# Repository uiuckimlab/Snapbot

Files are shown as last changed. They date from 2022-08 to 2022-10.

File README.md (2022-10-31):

# SNAPBOT 2.0
<div align="center">

</div>

-----------------
**Snapbot** is a reconfigurable legged robot to emulate configuration changes and various styles of legged locomotion. **Snapbot V2.0** has upgraded hardware to improve dynamical performance and robustness of the system for repetitive, and dynamical operations. 

Snapbot consists of a body and leg modules. The body modules includes a computer, batteries, electronic circuit boards, and a camera module. The camera module has 2-DOF, which can be used to recognize the robot's configuration or see surroundings. The leg module can be attached and detached to the body using magnetic connection, so it doesn't need any fastners but the docking structure ensures sturdy connection even during an impulsive motions. 

In this repository, we provide STL files and a BOM that is necessary to build the Snapbot V2.0 hardware, MATLAB Simscape simulation models, ROS package for the hardware, and URDF of the robot. 

## Contents
1. [3D printing STL](#3d-printing-stl)
2. [MATLAB Simulation](#matlab-simulation)
3. [ROS Package](#ros-package)
4. [Related Work](#related-work)
5. [Citation](#citation)

## 3D printing STL
STL files are provided in "3D printing STL" folder. The parts can be printed using most of 3D printing methods (FDM, SLS, SLA, etc.). The folder also contains the BOM (Bill of Materials) which lists the off-the-shelf components needed to build the Snapbot2.0 hardware. 

Currently there are two different head designs:
1. Default head


2. Babyface head


"3D printing STL/Head" folder has subfolders of two heads including the head cover and motor brackets. 

## MATLAB Simulation


Simulation model for Snapbot V2 was created using MATLAB Simscape multi-body (MATLAB 2021a). There are three simulations models for 2 leg, 4 leg, and 6 leg configuration with the motion generator implemented in the [paper](#citation).

## ROS Package
ROS package used to operate Snapbot V2 is provided with URDF file and meshes. By executing launch file "snapbot.launch", the robot can be teleoperated using keyboard inputs.

## Related Work

- [**Snapbot: A reconfigurable legged robot**](https://ieeexplore.ieee.org/abstract/document/8206477)
- [**Trajectory-based Probabilistic Policy Gradient for Learning Locomotion Behaviors**](https://ieeexplore.ieee.org/abstract/document/8794207)
- [**Automated Deep Reinforcement Learning Environment for Hardware of a Modular Legged Robot**](https://ieeexplore.ieee.org/abstract/document/8442201)
 
<!-- @INPROCEEDINGS{8206477,
  author={Kim, Joohyung and Alspach, Alexander and Yamane, Katsu},
  booktitle={2017 IEEE/RSJ International Conference on Intelligent Robots and Systems (IROS)}, 
  title={Snapbot: A reconfigurable legged robot}, 
  year={2017}}

@INPROCEEDINGS{8442201,  
  author={Ha, Sehoon and Kim, Joohyung and Yamane, Katsu},  
  booktitle={2018 15th International Conference on Ubiquitous Robots (UR)},   
  title={Automated Deep Reinforcement Learning Environment for Hardware of a Modular Legged Robot},   
  year={2018}}

@INPROCEEDINGS{8794207,  
  author={Choi, Sungjoon and Kim, Joohyung},  
  booktitle={2019 International Conference on Robotics and Automation (ICRA)},   
  title={Trajectory-based Probabilistic Policy Gradient for Learning Locomotion Behaviors},   
  year={2019}}
 -->

## Citation
```
@INPROCEEDINGS{9341279,  
  author={Gim, Kevin G. and Kim, Joohyung},  
  booktitle={2020 IEEE/RSJ International Conference on Intelligent Robots and Systems (IROS)},   
  title={Snapbot V2: a Reconfigurable Legged Robot with a Camera for Self Configuration Recognition},   
  year={2020}
}
```
Link: https://ieeexplore.ieee.org/abstract/document/9341279

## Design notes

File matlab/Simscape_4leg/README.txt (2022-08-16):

Simscape Multibody Contact Forces Library
Copyright 2014-2019 The MathWorks, Inc.

This library contains contact force models for use with Simscape Multibody.
They can be used for intermittent contact (parts bouncing off each other)
and persistent contact (parts resting on each other).  

You are welcome to use this library in your own projects. If you need to 
include the library in your own project, run >> CFL_SaveLibsOnly.m from 
the root directory of your local repository.  Only the critical files
will be copied to a folder "CFL_Libs", and you can cut-and-paste that
to your own local project.  Please cite

General approach for using this library:
   1. Identify the parts in your system that will hit each other during simulation

   2. Figure out which edges or surfaces will touch.  
      The contact models provided allow you to model contact between combinations
      of connected circular arcs with straight lines (2D) 
      and spheres with flat planes or cylinders (3D).

   3. Add reference frames for the lines and arcs that will touch.

   4. Add the correct contact force model between the two frames.

See the examples to understand how they are used.

Recommendations:
   1. Start with stiffness of 1e4 and damping of 1e2 and adjust from there.
   2. Use solver ode15s, Relative Tolerance = 1e-4, Absolute Tolerance = 1e-5
       and set the maximum step size to 1e-2.
   3. If you get unexpected behavior (parts flying through one another, 
       system gaining energy) your tolerances are not small enough.
       Reduce tolerances by a factor of 10 and max step size by a factor of 10
       until you get expected behavior.  Reducing stiffness and increasing damping
       can also help.

#########  Release History  #########
v 4.1(R2019a)   Mar 2019       Updated v4.1 for R2019a
                               Minor changes to accommodate physical signal units

v 4.1(R2018b)   Nov 2018       Added two examples
     (R2018a)   
     (R2017b)   1. New example Caster_4_Whl.slx
     (R2017a)      Models a four-wheel cart with casters on front wheels 
     (R2016b)
     (R2016a)   2. New example sm_build_spheres_in_sphere
     (R2015b)      MATLAB code to automatically assemble a model that has 
     (R2015a)      a user-defined number of spheres inside a sphere with
                   contact forces between all inner spheres and between 
                   inner spheres and outer sphere.

v 4.1(R2018b)   Sep 2018       Updated v4.1 for R2018b
                               All v4p1 have updated Extr_Data_Cam_Roller_Curve.m

     (R2018a)   Mar 2018       Tread example, walking robot example 
     (R2017b)
     (R2017a)   1. Adjusted Sphere to Belt Force (in 3D, Composite Forces)
     (R2016b)      Changed orientation of reference frame for the two
     (R2016a)      Sphere to Tube Enabled Forces. Z-axis flipped 180 deg
     (R2015b)      so that vx and wz inputs have the same sign. 
     (R2015a)   
                2. Adjusted sm_tread_drive example.slx
                   Uses adjusted Sphere to Belt Force, test sequence altered
                   to show turning and show both treads striking bump in 
                   forward and reverse. 

                3. New example sm_robot_6legs_4bar.slx 
                   Models 6-legged robot. Legs on each side are a pair of
                   connected four-bar linkages. Shows how to model robot
                   walking on uneven surface.   

                4. Added CFL_contact_setModel.m
                   Function to select force law in all contact forces in model.

                5. Additions to support Parts_Lib.slx 
                   Extrusion file Extr_Data_TriangleRounded_Holes.m and 
                   various images for masking parts.

v 4.0(R2018a)	Mar 2018       Updated for R2018a
     (R2017b)
     (R2017a)   1. Added Sphere to Tube Enabled Force
     (R2016b)      Sphere to Tube force that can be enabled/disabled
     (R2016a)      and can be used to model the ends of a driven conveyor belt.
     (R2015b)
     (R2015a)   2. Added Sphere to Belt Force (in 3D, Composite Forces)
                   Used to models spheres on a moving conveyor belt.  Can
                   also be used to model vehicles that ride on treads
                   like a bulldozer.  See sm_tread_drive  

                3. New examples sm_tread_drive, Frict3D_Balls_on_Driven_Tube 
                   These examples use Sphere to Tube Enabled Force and
                   Sphere to Belt Force. 

                4. Added sm_ball_bearing_testrig example
                   Models a ball bearing with variants that use
                   Common Gear Constraint (ideal) and contact forces
                   (permits vibration).

                5. Added extrusion script Extr_Data_Block_NotchCircle.m 
                   Used to calculate cross-sectional profile for inner and
                   outer race in Ball Bearing Testrig example

v 3.9 (R2017b)	Jan 2018       Added Cam Roller Constraint
                1. Added Cam Roller Constraint.  
                   Uses Point-on-Curve Constraint to model circular
                   roller on a cam with arbitrary profile.

                2. Added Extr_Data_Cam_Roller_Curve.m to calculate
                   path of Point-on-Curve Constraint.

                3. Added Cam_Follower_Constraint example.

v 3.8 (R2017b)	Sept 2017      Updated for R2017b

v 3.7 (R2017a)	July 2017      Sphere to Cone Force, many fixes
      (R2016b)		           Library saved in versions R2015b through R2017a
      (R2016a)
      (R2015b)
                1. Added Sphere to Cone Force.  Contact force is active on
		        inside and outside of cone.  Also added extrusion script
		        Extr_Data_Frustrum_Conical.m and example 
                Coll3D_08_Ball_in_Spinning_Cone.slx

                2. Sphere to Tube Force - fixed relative velocity calculation in
                Contact_Forces_Lib/3D/Sphere to Tube Force/Forces/Ff/vTan
                Previous releases delivered incorrect results if the cylinder
                could spin.  Added new example Coll3D_07_Balls_and_Sliding_Tube.slx

                3. Extr_Data_Box.m: functional change, parameters are full width
                and height instead of half width and half height.  Affected
                parameters within a few examples, such as Spinning Boxes

                4. Extr_Data_Cam.m: Changed to Extr_Data_Cam_Circles.m, which has
                two additional parameters (radii of holes).  Affected example
                Cam Follower and the UI for parameterizing the cam.

                5. Many 2D contact forces have been modified so that they
		        no longer refer to the World frame.  This permits them to be
                used in any plane, not just the x-y plane.

                6. Circle to Ring Force: calculations adjusted to use consistent
                distance to contact point for circle and ring.  May result in
                minor changes to simulation results.

                7. Mask commands adjusted - eliminated imread(), use option
                "Opaque with ports" (R16a and above), and other settings.

v 3.6 (R2017a)	Mar  2017       Updated for R2017a
      (R2016b)	
                1. New example: Ball on Wheel with Controller (2D Friction Examples)
                   Models a ball balanced on a wheel.
                2. Removed MATLAB variables from blocks in Contact_Forces_Lib.slx
                   Some library elements contained MATLAB variables in the dialog box
                   parameters on the Dimensions and Visual tab.  These were replaced
                   with hardcoded default values to avoid warnings about undefined variables.
                3. Additional parameters were added to the Sphere block in Parts_Lib.slx 
                   to enable the marks to be shown or hidden per axis. 
                4. New script CFL_SaveLibsOnly.m that copies only the critical files 
        		   of this repository to a new folder so you can include them in
                   your own project.

v 3.5 (R2016b)	Jan  2017	3D Composite Forces, Sphere-to-Plane Enabled
                1. Added Face-to-Plane in 3D/Composite Forces.  This is useful for
                   two flat square surfaces that may contact each other at arbitrary 
                   angles.  It assumes no edges will intersect (one square is 
                   significantly larger than the other
                2. Added Face-to-Belt-Faces forces in 3D/Composite Forces.  This is
                   useful for modeling 3D boxes on conveyor belts where only one
                   face of the box will encounter the belt.  It accepts the 
                   speed of the belt as an input signal (vx and/or vy)
                3. Added Sphere-to-Plane Enabled Force.  This is used within the
                   composite force´Face-to-Belt-Faces composite force
                4. Added example Gripper with Conveyor Belts (3D Applications). 
                   Uses the new forces to model a box that is transferred by a 
                   gripper between two conveyor belts.  One belt brings the box
                   to the gripper, the other moves it away.

		Additional parameters were added to the Cylinder block 
                in Parts_Lib.slx to enable arbitrary colors for the cylinders.

v 3.4 (R2016b)	Sep  2016	Updated for R2016b
		1. Fixed outputs for Circle-to-Ring, Sphere-to-Tube, Sphere-to-Plane
		   Force output signals for these signals now go to zero when 
		   circle/sphere leaves active range for force, where active range is 
		   an arc of the ring/tube or length of the plane. Previously, the
		   measured value for the force would be held if the force was active
		   as the circle/sphere left the active range for the force.

		2. Copy for Merge block added in Sphere-to-Plane block
		   This block is necessary in some configurations.

v 3.3 (R2016a)	Apr  2016	Added optional visualization for contact surfaces
		The surfaces associated with the contact forces can now be visualized.	
		This helps you confirm you have oriented the surfaces properly and
		defined them to be an appropriate length or active range of angles.

		All contact forces now have an additional tab labeled "Visual".  On
		this tab you can enable a visualization of the surface, which is done
		using a Solid with density set to 0.  For the 2D contact forces you 
		will need to define the length of the surface along the z-axis of
		the contact force and it is used for visualization purposes only. 
		You can show/hide all contact surfaces in the model using the
		new function CFL_visual_setOnOff.m in the Scripts_Data directory.

		Additionally in this release, a number of plotting scripts have been
		added to the examples, and in many cases the variables used by
		the example were moved to the Model Workspace.

v 3.2 (R2016a)	Mar  2016	Disabled zero crossings in some Abs blocks
      (R2015b)  Affects Circle-to-Finite Line, Sphere to Finite Plane
		The zero-crossings in Abs blocks used to check the displacement
                of the circle/sphere reference frame from the line/plane
		reference frame along the line/surface (y / xy) direction is
		not necessary.  When the line/plane can move along the (y / xy)
 		direction, it can lead to excessive zero crossings, slowing down
		the simulation.

v 3.1 (R2016a)	Mar  2016	Renamed Simscape Multibody Contact Forces Library
		1. Geneva drive model imported from CAD is now parameterized

v 3.0 (R2015b)  Sept 2015	Updated to R2015b

v 3.0 (R2015a)  July 2015	3D models added
                1. Sphere-to-Sphere, Sphere-in-Sphere, Sphere-to-Plane, 
                   Sphere-to-Tube added, all with optional friction model
                2. Added 3D collision and friction examples
		3. Added Two Wheel Robot example (3D Applications)

                (2D Models)
                4. Modified 2D enabled forces
		   ** Change from v2.0 -- may require you to update your models ** 
                   Modified Circle to Circle Force Enabled, 
                   Circle to Finite Line Force Enabled to use a bus as the
                   input signal instead of signal input.  Bus permits user to
                   optionally define enabled/disabled, and to set velocity
                   perpendicular to normal force (vy).  Primary use is for ideal 
                   models of conveyor belts.
                5. Added 2D/Composite forces (Box to Box force, Box to Belt force)
                6. Added Belts_01_Two_Belts.slx (simple conveyor belt example)
                
                Documentation, Dialog boxes
                7. Updates to all dialog boxes (added images, fixed prompts and description)
                8. Documentation revised                

v 2.0 (R2014a)  September 2014	Friction model added
                1. Added optional friction model (Stick-Slip Continuous)
		   to Circle to Circle, Circle to Finite Line, Circle to Ring
                2. Added all Friction_* examples 
                3. Added Spinning Boxes example 
                   Shows box-to-box contact force
                4. Fixed callback commands, all contact force blocks
		   Set variant in Initialization commands instead of mask callbacks
                5. Fixed Circle to Finite Line, Circle to Finite Line Enabled
                   Force on line was applied in wrong reference frame

v 1.0 (R2014a)  August 2014     Initial release.
		Circle-Circle (Enabled), Circle-Line (Enabled), Circle-Ring
		7 Simple, Cam Follower, Geneva Drive. Mini Golf compatible

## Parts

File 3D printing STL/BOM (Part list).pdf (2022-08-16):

Parts List

Leg
Part | Motor | Idler | Ball bearings
Model | Dynamixel XM430-W210-T (https://www.robotis.us/dynamixel-xm430-w210-t/) | Robotis HN12-I101 set (https://www.robotis.us/hn12-i101-set/) | SMR128ZZ A5 (http://www.metsorj.com/ProductDetails.asp?ProductCode=E4W336)
Quantity | 12 (2 per leg) | 12 (2 per leg) | 12 (2 per leg)

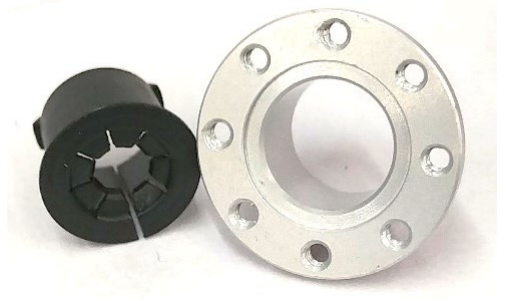
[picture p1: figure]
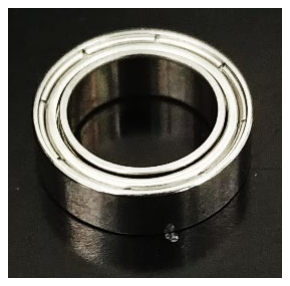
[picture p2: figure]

Image

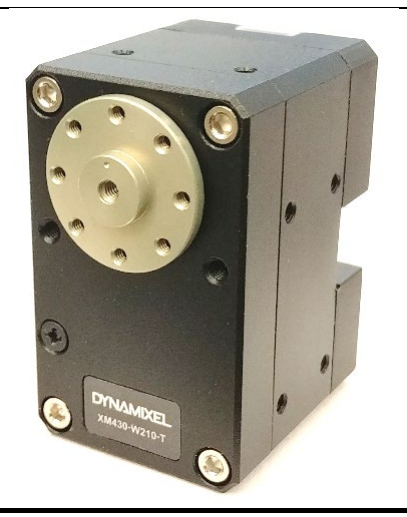
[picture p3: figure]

Custom Electronics
Wires
For connection ports
Part (for:) | Connector housing
Power board | Leg motor | Connection port
Model | Molex 0050375033 (https://www.digikey.com/en/products/detail/molex/0050375033/280419) | Molex 0510650300 (https://www.digikey.com/en/products/detail/molex/0510650300/403567) | Molex 0510650400 (https://www.digikey.com/en/products/detail/molex/0510650400/403568)
Quantity | 6 | 6 | 12

Image

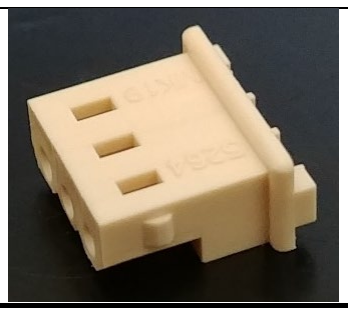
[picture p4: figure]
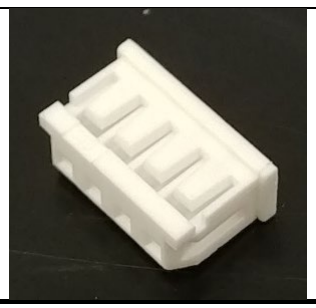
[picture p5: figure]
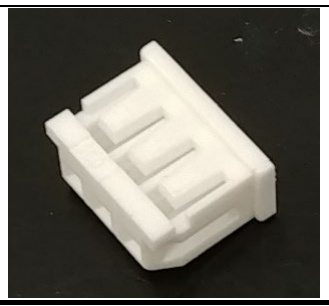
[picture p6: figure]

Part (for:) | Terminal
Connection port; leg motor | Power board
Model | Molex 0502128000 (https://www.digikey.com/en/products/detail/molex/0502128000/2524899) | Molex 0008701039 (https://www.digikey.com/en/products/detail/molex/0008701039/765268)
Quantity | 54 | 18

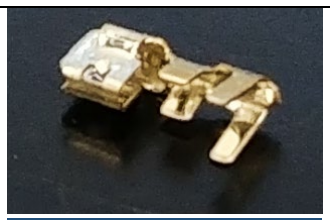
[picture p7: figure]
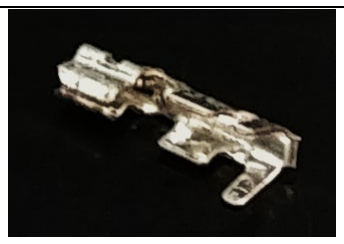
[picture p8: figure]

Image

***Following are intertwined and go into terminal block***

For power board / battery

Part | Battery connector
Model | Finware AMASS XT30U-M (https://www.tme.com/us/en-us/details/xt30u-m/dc-power-connectors/amass/)
Quantity | 2


Image

For regulators

Part (for:) | Connector housing | Terminal
5V regulator | 7.5V regulator | Both regulators
Model | JST EHR-3 (https://www.digikey.com/en/products/detail/jst-sales-america-inc/EHR-3/527225) | JST EHR-4 (https://www.digikey.com/en/products/detail/jst-sales-america-inc/EHR-4/527226) | JST SEH-001T-P0.6 (https://www.digikey.com/en/products/detail/jst-sales-america-inc/SEH-001T-P0-6/527267)
Quantity | 1 | 1 | 7

Image


Part (for:) | Connector header
5V regulator | 7.5V regulator
Model | JST B3B-EH-A(LF)(SN) (https://www.digikey.com/en/products/detail/jst-sales-america-inc/B3B-EH-A-LF-SN/926521) | JST B4B-EH-A(LF)(SN) (https://www.digikey.com/en/products/detail/jst-sales-america-inc/B4B-EH-A-LF-SN/758748)
Quantity | 1 | 1


Image

Connection Ports

Part | Spring-loaded connector (male) | Spring-loaded connector (female) | Connector header
Model | Mill-Max 823-22-008-10- (https://www.digikey.com/en/products/detail/mill-max-manufacturing-corp/823-22-008-10-002101/1146974)002101 (https://www.digikey.com/en/products/detail/mill-max-manufacturing-corp/823-22-008-10-002101/1146974) | Mill-Max 419-10-208-00- (https://www.digikey.com/en/products/detail/mill-max-manufacturing-corp/419-10-208-00-006000/5176111)006000 (https://www.digikey.com/en/products/detail/mill-max-manufacturing-corp/419-10-208-00-006000/5176111) | Molex 0532530470 (https://www.digikey.com/en/products/detail/molex/0532530470/965998)
Quantity | 6 | 6 | 12

Image


The connection ports also require a custom PCB. A CAD model and a circuit diagram are provided. Twelve of these PCBs need to be printed.

Power Board

Part | Connector header (leg) | Connector header (camera) | Terminal block
Model | Molex 0022035035 (https://www.digikey.be/product-detail/en/molex/0022035035/900-0022035035-ND/403302) | Molex 0532530370 (https://www.digikey.com/en/products/detail/molex/0532530370/965997) | TE Connectivity 282834-2 (https://www.digikey.com/en/products/detail/te-connectivity-amp-connectors/282834-2/1150135)
Quantity | 7 | 1 | 2

Image


The power board is a custom PCB. A CAD model and a circuit diagram are provided. Only one of these PCBs is required.

Body
Orange Pi Lite
SD card (16 GB)
Camera
U2D2 dongle
Voltage regulators (7.5V, 5V)

Other necessary stuff

22 AWG wire
18 AWG wire (for battery connector) (Wire with female connector for orange pi) Solder
Soldering iron
Screws
Magnets
Wire crimper
Wire cutter/stripper
Allen key: M2, M2.5, M3
Pliers
3d printer + material
Heat shrink / tape
Hot glue gun

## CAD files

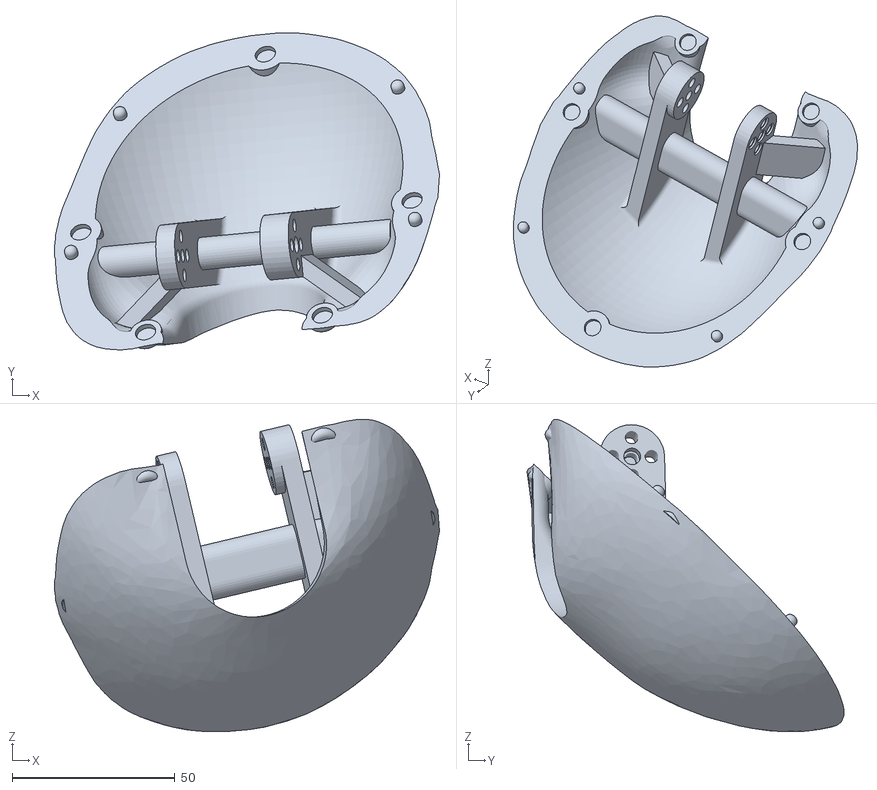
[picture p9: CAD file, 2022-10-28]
3D printing STL/Head/Babyface/Babyface_bracket.STL
118.2 x 97.3 x 95.9

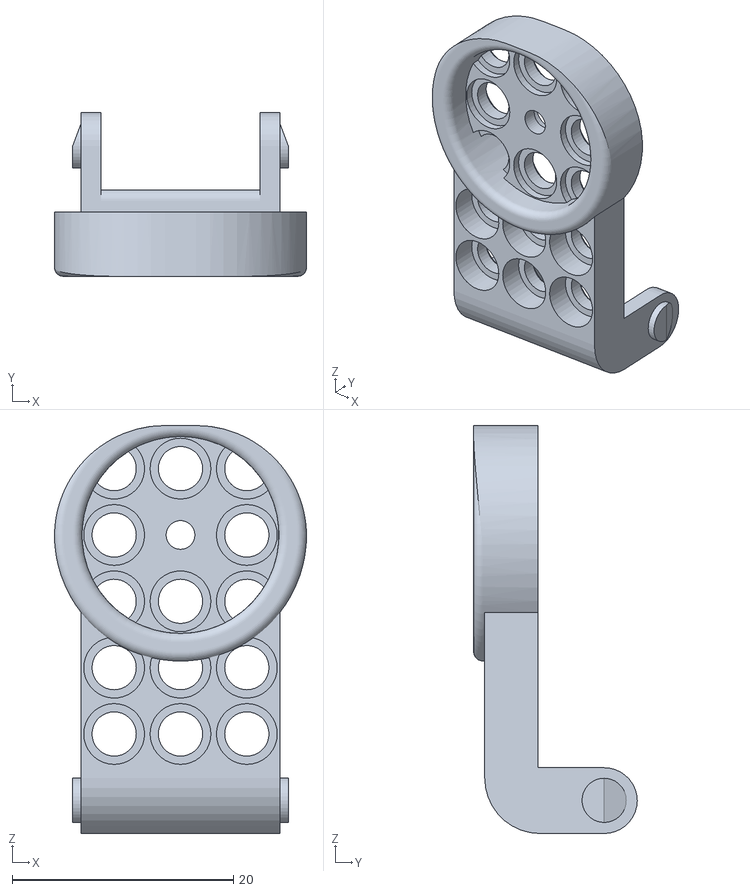
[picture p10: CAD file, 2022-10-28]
3D printing STL/Head/Default/Camera_plate_yaw.STL
22.8 x 14.8 x 36.9

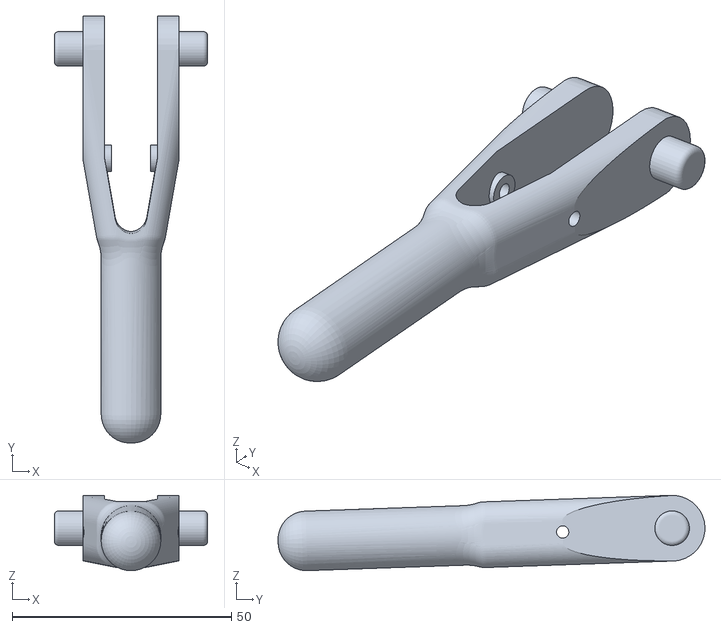
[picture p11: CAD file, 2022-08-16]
3D printing STL/Leg_part_05.STL
35.0 x 97.5 x 17.2

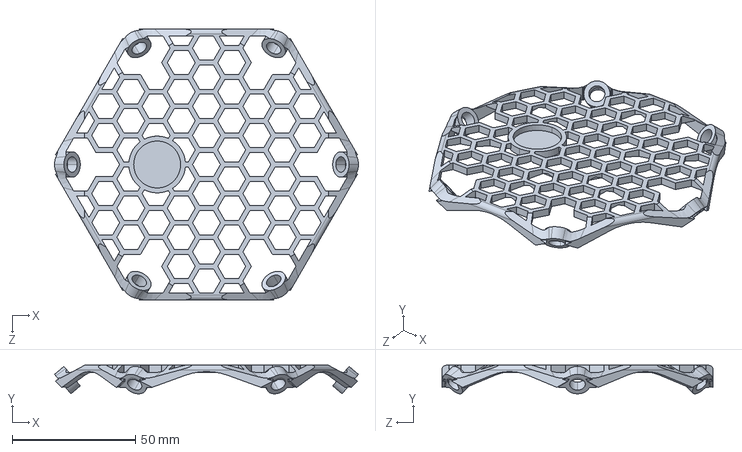
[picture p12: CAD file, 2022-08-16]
matlab/Simscape_2leg/cover_IMU_Default_sldprt.STEP
123.2 x 11.6 x 110.0 mm

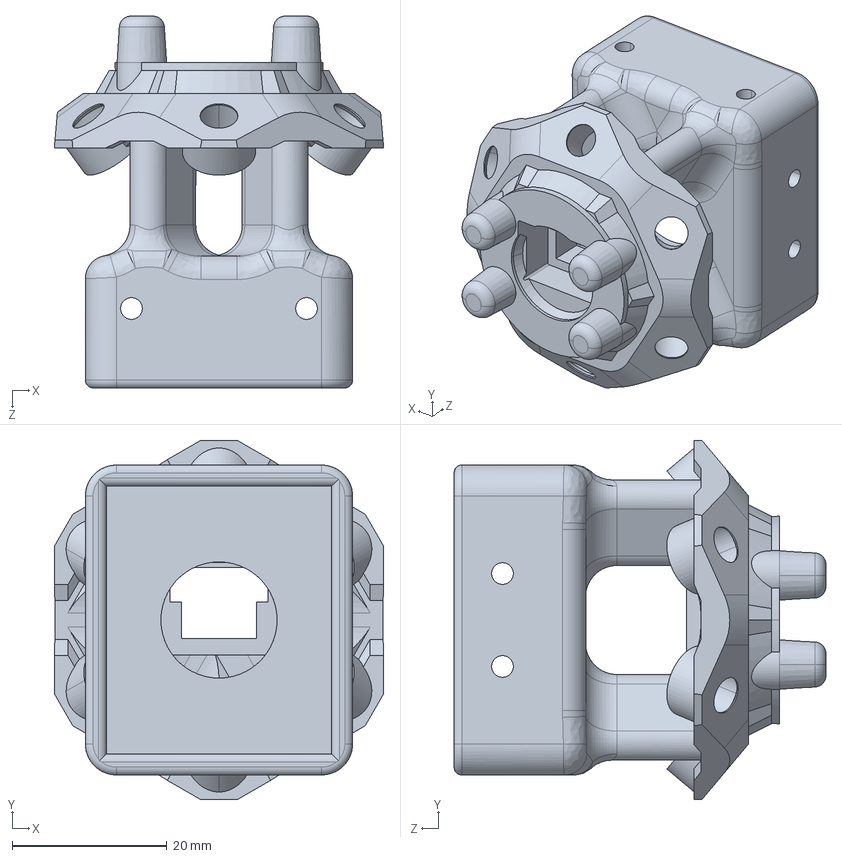
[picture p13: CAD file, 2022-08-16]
matlab/Simscape_6leg/Leg_part_01_yaw_Default_sldprt.STEP
42.5 x 46.3 x 48.0 mm

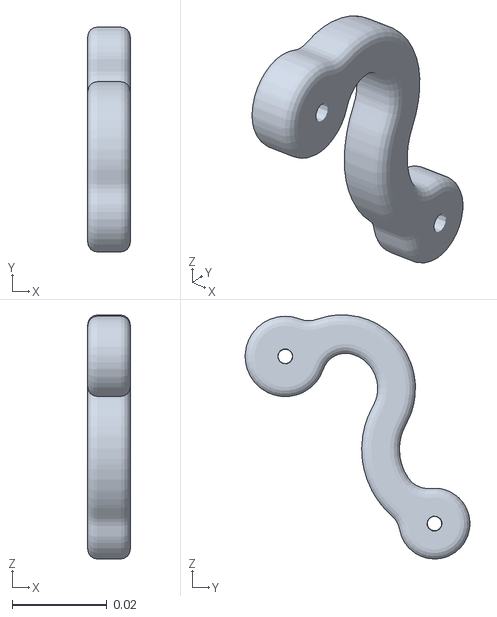
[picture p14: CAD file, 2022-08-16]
meshes/Leg_module_4_4bar.STL
0.009 x 0.0476 x 0.0516

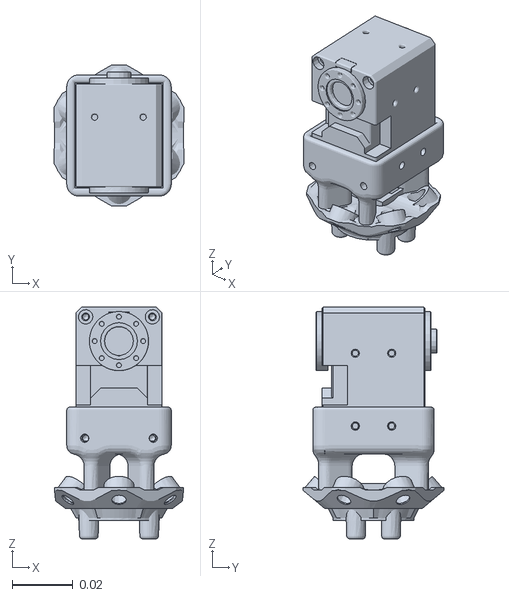
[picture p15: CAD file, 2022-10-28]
URDF/URDF_babyface(10282022)/Snapbot_V2.0.SLDASM/meshes/Leg_module_1_1.STL
0.0427 x 0.0466 x 0.0765

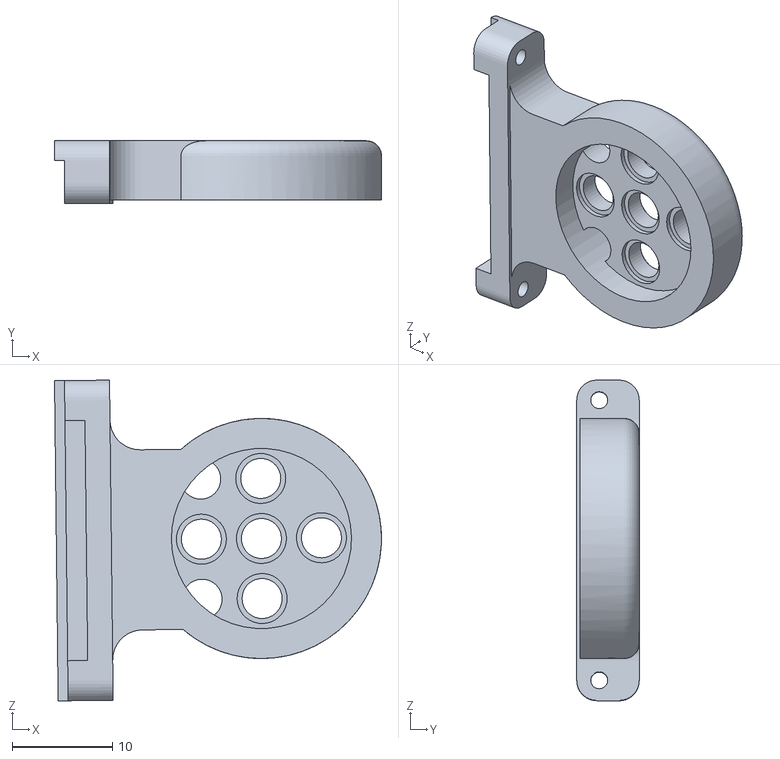
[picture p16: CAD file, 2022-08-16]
3D printing STL/Camera_bracket_2.STL
32.7 x 6.25 x 32.1

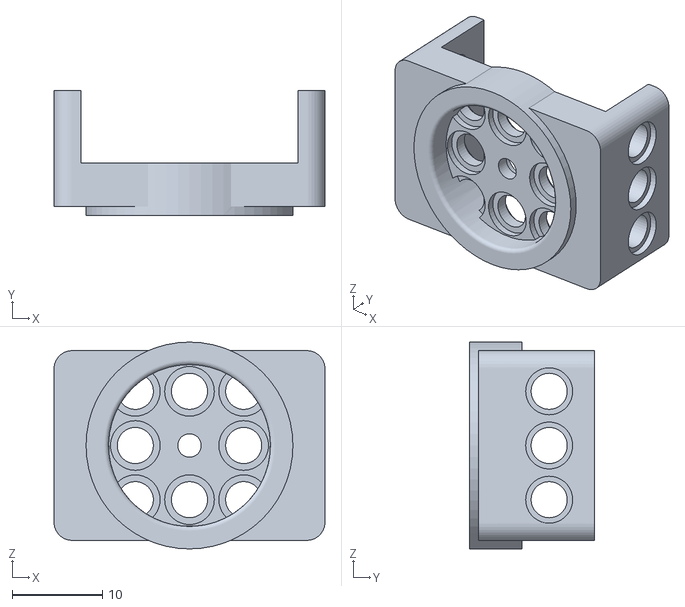
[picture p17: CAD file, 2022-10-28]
3D printing STL/Head/Babyface/Yaw_motor_bracket.STL
30.0 x 13.8 x 22.9

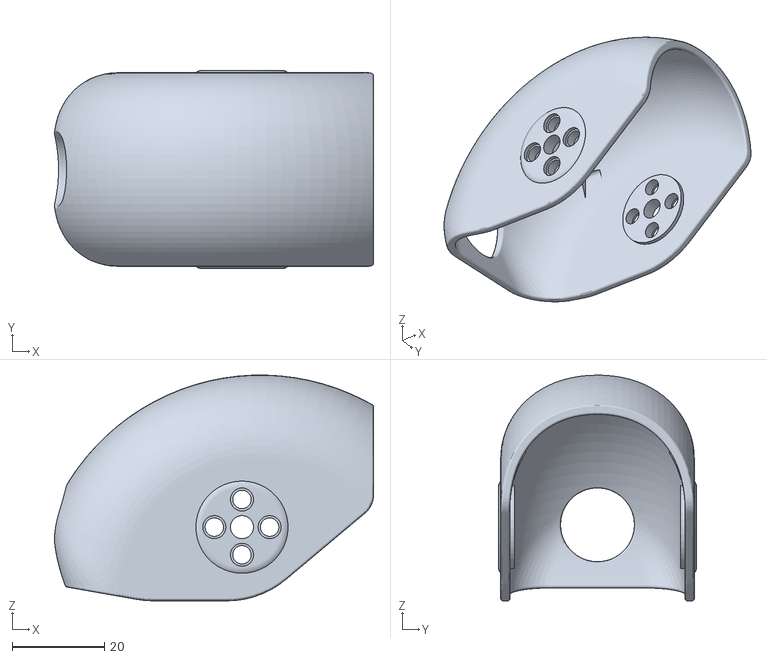
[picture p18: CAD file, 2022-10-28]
3D printing STL/Head/Default/Snapbot_Head.STL
69.2 x 43.0 x 49.0

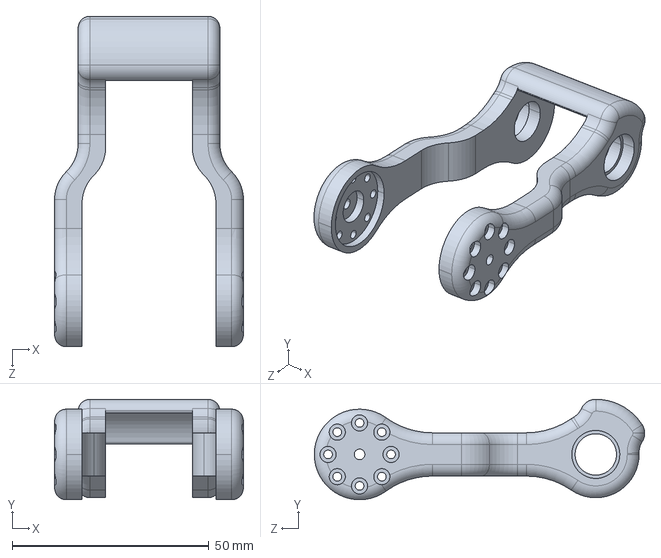
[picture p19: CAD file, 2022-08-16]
matlab/Simscape_2leg/Leg_part_04_Default_sldprt.STEP
48.0 x 25.5 x 83.9 mm

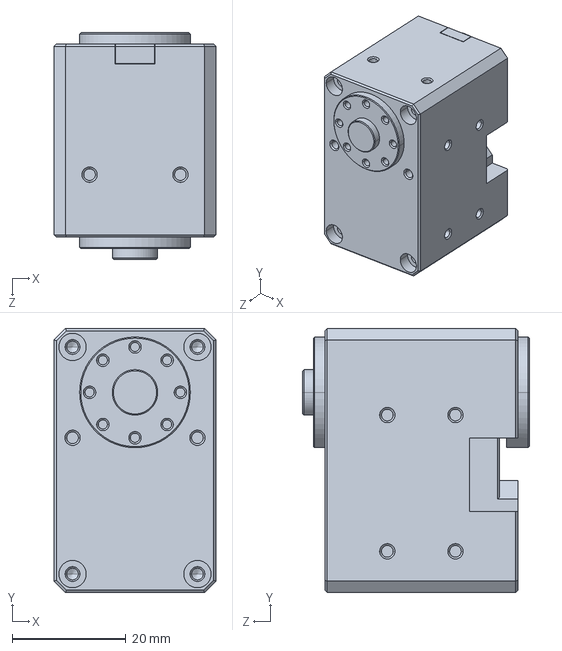
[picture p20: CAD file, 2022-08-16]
matlab/Simscape_6leg/v4_Hyb_X-430_IDLE_uncut_Default_sldprt.STEP
28.5 x 46.5 x 39.9 mm

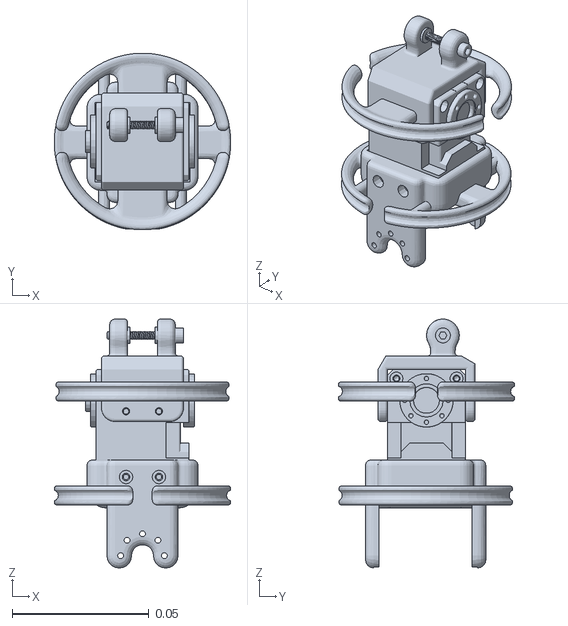
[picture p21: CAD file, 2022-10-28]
URDF/URDF_Default (10282022)/Snapbot_V2.0.SLDASM/meshes/Leg_module_1_2.STL
0.0645 x 0.0645 x 0.091

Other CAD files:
matlab/Simscape_4leg/cover_Default_sldprt.STEP
URDF/URDF_Default (10282022)/Snapbot_V2.0.SLDASM/meshes/Leg_module_2_4bar.STL
matlab/Simscape_4leg/cover_IMU_Default_sldprt.STEP
meshes/Leg_module_6_4bar.STL
URDF/URDF_babyface(10282022)/Snapbot_V2.0.SLDASM/meshes/Leg_module_2_4bar.STL
3D printing STL/Body - cover_V4-1.STL
3D printing STL/Body - cover_top_V4-1.STL
3D printing STL/Camera_bracket_1.STL
3D printing STL/Camera_bracket_3.STL
3D printing STL/Camera_cover.STL
3D printing STL/Head/Babyface/Babyface_Face.STL
3D printing STL/Head/Default/Camera_bracket_pitch_1.STL
3D printing STL/Head/Default/Camera_bracket_pitch_2.STL
3D printing STL/Leg_part_01.STL
3D printing STL/Leg_part_02.STL
3D printing STL/Leg_part_03.STL
3D printing STL/Leg_part_04.STL
3D printing STL/Leg_part_06.STL
URDF/URDF_Default (10282022)/Snapbot_V2.0.SLDASM/meshes/Body.STL
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

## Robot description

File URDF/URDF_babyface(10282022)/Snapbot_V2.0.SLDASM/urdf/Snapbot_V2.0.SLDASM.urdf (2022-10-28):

<?xml version="1.0" encoding="utf-8"?>
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
<robot name="Snapbot_V2.0.SLDASM">
  <link name="Body">
    <inertial>
      <origin xyz="0.000698393115871002 0.000288945802796733 0.0080342370525136" rpy="0 0 0" />
      <mass value="0.243375116892044" />
      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
    </inertial>
    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
  </link>
  <link name="Camera_module_1">
    <inertial>
      <origin xyz="-0.000174104745675234 0.000380109596667467 0.0231270475088353" rpy="0 0 0" />
      <mass value="0.0193486685182062" />
      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
    </inertial>
    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
  </link>
  <joint name="camera_1" type="continuous">
    <origin xyz="0 0 0.05" rpy="0 0 2.61799387799149" />
    <parent link="Body" />
    <child link="Camera_module_1" />
    <axis xyz="0 0 1" />
  </joint>
  <link name="Camera_module_2">
    <inertial>
      <origin xyz="0.00436630099388993 0.00301719279420027 0.0506803900992624" rpy="0 0 0" />
      <mass value="0.486270044594427" />
      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
    </inertial>
    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
  </link>
  <joint name="camera_2" type="continuous">
    <origin xyz="0 0 0.0183294742460734" rpy="-0.00940777862508587 0.0162930683068517 -7.6643050616781E-05" />
    <parent link="Camera_module_1" />
    <child link="Camera_module_2" />
    <axis xyz="0.500000000000001 -0.866025403784438 0" />
  </joint>
  <link name="Leg_module_1_1">
    <inertial>
      <origin xyz="-7.13724657916415E-08 0.000373799301046029 0.0154182546673216" rpy="0 0 0" />
      <mass value="0.0631785349056668" />
      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
    </inertial>
    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
  </link>
  <joint name="leg_1_1" type="fixed">
    <origin xyz="-0.0389249999999995 -0.0674200776846189 0.0103294742460734" rpy="1.5707963267949 0 -0.52359877559829" />
    <parent link="Body" />
    <child link="Leg_module_1_1" />
    <axis xyz="0 0 0" />
  </joint>
  <link name="Leg_module_1_2">
    <inertial>
      <origin xyz="-0.000290776360641745 0.000350553903850227 0.0424303561818182" rpy="0 0 0" />
      <mass value="0.0824270440491864" />
      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
    </inertial>
    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
  </link>
  <joint name="leg_1_2" type="continuous">
    <origin xyz="0 0 0.03725" rpy="0 0 0" />
    <parent link="Leg_module_1_1" />
    <child link="Leg_module_1_2" />
    <axis xyz="0 1 0" />
  </joint>
  <link name="Leg_module_1_3">
    <inertial>
      <origin xyz="2.45741484106166E-09 0.000972843111612401 0.036226536467209" rpy="0 0 0" />
      <mass value="0.0151486232431239" />
      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
    </inertial>
    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
  </link>
  <joint name="leg_1_3" type="continuous">
    <origin xyz="0 0.00029999999999997 0.05675" rpy="-0.0100573048452913 0 0" />
    <parent link="Leg_module_1_2" />
    <child link="Leg_module_1_3" />
    <axis xyz="1 0 0" />
  </joint>
  <link name="Leg_module_1_4">
    <inertial>
      <origin xyz="4.20295677225763E-05 -0.039054256810963 -0.001354432069402" rpy="0 0 0" />
      <mass value="0.0147333532003768" />
      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
    </inertial>
    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
  </link>
  <joint name="leg_1_4" type="continuous">
    <origin xyz="0 -0.000603428117922688 0.0599969655441553" rpy="-0.0105798453585739 0 0" />
    <parent link="Leg_module_1_3" />
    <child link="Leg_module_1_4" />
    <axis xyz="1 0 0" />
  </joint>
  <link name="Leg_module_1_4bar">
    <inertial>
      <origin xyz="-0.000153041712575408 -0.0147990308191147 0.0229851342034179" rpy="0 0 0" />
      <mass value="0.00683592925491238" />
      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
    </inertial>
    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
  </link>
  <joint name="leg_1_4bar" type="continuous">
    <origin xyz="0 0.00629999999999993 0.0804999999999999" rpy="-0.0165784581965256 0 0" />
    <parent link="Leg_module_1_2" />
    <child link="Leg_module_1_4bar" />
    <axis xyz="1 0 0" />
  </joint>
  <link name="Leg_module_2_1">
    <inertial>
      <origin xyz="-6.95475167594717E-08 0.00037379623691287 0.0154182547266335" rpy="0 0 0" />
      <mass value="0.063178534807664" />
      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
    </inertial>
    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
  </link>
  <joint name="leg_2_1" type="fixed">
    <origin xyz="0.038925000000001 -0.0674200776846179 0.0103294742460733" rpy="1.5707963267949 0 0.52359877559831" />
    <parent link="Body" />
    <child link="Leg_module_2_1" />
    <axis xyz="0 0 0" />
  </joint>
  <link name="Leg_module_2_2">
    <inertial>
      <origin xyz="-0.000290786260265109 0.000350550447493953 0.0424303491067431" rpy="0 0 0" />
      <mass value="0.0824270292833377" />
      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
    </inertial>
    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
  </link>
  <joint name="leg_2_2" type="continuous">
    <origin xyz="0 0 0.03725" rpy="0 0 0" />
    <parent link="Leg_module_2_1" />
    <child link="Leg_module_2_2" />
    <axis xyz="0 1 0" />
  </joint>
  <link name="Leg_module_2_3">
    <inertial>
      <origin xyz="6.11769995773059E-10 0.000972841972894574 0.0362265364557568" rpy="0 0 0" />
      <mass value="0.0151486232431239" />
      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
    </inertial>
    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
  </link>
  <joint name="leg_2_3" type="continuous">
    <origin xyz="0 0.000299999999999996 0.0567499999999999" rpy="-0.0100573048453112 0 0" />
    <parent link="Leg_module_2_2" />
    <child link="Leg_module_2_3" />
    <axis xyz="1 0 0" />
  </joint>
  <link name="Leg_module_2_4">
    <inertial>
      <origin xyz="4.19939626801757E-05 -0.0390541987134747 -0.00135443548203865" rpy="0 0 0" />
      <mass value="0.0147333946079412" />
      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
    </inertial>
    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
  </link>
  <joint name="leg_2_4" type="continuous">
    <origin xyz="0 -0.000603428117910471 0.0599969655441548" rpy="-0.0105798453581945 0 0" />
    <parent link="Leg_module_2_3" />
    <child link="Leg_module_2_4" />
    <axis xyz="1 0 0" />
  </joint>
  <link name="Leg_module_2_4bar">
    <inertial>
      <origin xyz="-0.000153041712573354 -0.0147990308191101 0.0229851342034186" rpy="0 0 0" />
      <mass value="0.00683592925491239" />
      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
    </inertial>
    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
  </link>
  <joint name="leg_2_4bar" type="continuous">
    <origin xyz="0 0.00629999999999995 0.0805" rpy="-0.0165784581965541 0 0" />
    <parent link="Leg_module_2_2" />
    <child link="Leg_module_2_4bar" />
    <axis xyz="1 0 0" />
  </joint>
  <link name="Leg_module_3_1">
    <inertial>
      <origin xyz="-7.06608178473466E-08 0.000373797728506917 0.0154182586742905" rpy="0 0 0" />
      <mass value="0.0631785313638385" />
      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
    </inertial>
    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
  </link>
  <joint name="leg_3_1" type="fixed">
    <origin xyz="0.0778499999999993 0 0.0103294742460734" rpy="1.5707963267949 0 1.5707963267949" />
    <parent link="Body" />
    <child link="Leg_module_3_1" />
    <axis xyz="0 0 0" />
  </joint>
  <link name="Leg_module_3_2">
    <inertial>
      <origin xyz="-0.000290780437123685 0.000350551822572993 0.0424303356191464" rpy="0 0 0" />
      <mass value="0.0824272438246167" />
      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
    </inertial>
    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
  </link>
  <joint name="leg_3_2" type="continuous">
    <origin xyz="0 0 0.03725" rpy="0 0 0" />
    <parent link="Leg_module_3_1" />
    <child link="Leg_module_3_2" />
    <axis xyz="0 1 0" />
  </joint>
  <link name="Leg_module_3_3">
    <inertial>
      <origin xyz="1.53462381789992E-09 0.00170127905765847 0.0361996388039809" rpy="0 0 0" />
      <mass value="0.0151486257339542" />
      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
    </inertial>
    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
  </link>
  <joint name="leg_3_3" type="continuous">
    <origin xyz="0 0.000300000000000003 0.0567499999999997" rpy="0.0100573048452967 0 0" />
    <parent link="Leg_module_3_2" />
    <child link="Leg_module_3_3" />
    <axis xyz="1 0 0" />
  </joint>
  <link name="Leg_module_3_4">
    <inertial>
      <origin xyz="4.20490632792337E-05 -0.039076824241083 0.000258194696472008" rpy="0 0 0" />
      <mass value="0.0147334003564446" />
      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
    </inertial>
    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
  </link>
  <joint name="leg_3_4" type="continuous">
    <origin xyz="0 0.000603428117812372 0.0599969655441564" rpy="0.0105798453584752 0 0" />
    <parent link="Leg_module_3_3" />
    <child link="Leg_module_3_4" />
    <axis xyz="1 0 0" />
  </joint>
  <link name="Leg_module_3_4bar">
    <inertial>
      <origin xyz="-0.000153041712520068 -0.0140289201388825 0.0234631009730389" rpy="0 0 0" />
      <mass value="0.00683592925491239" />
      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
    </inertial>
    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
  </link>
  <joint name="leg_3_4bar" type="continuous">
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

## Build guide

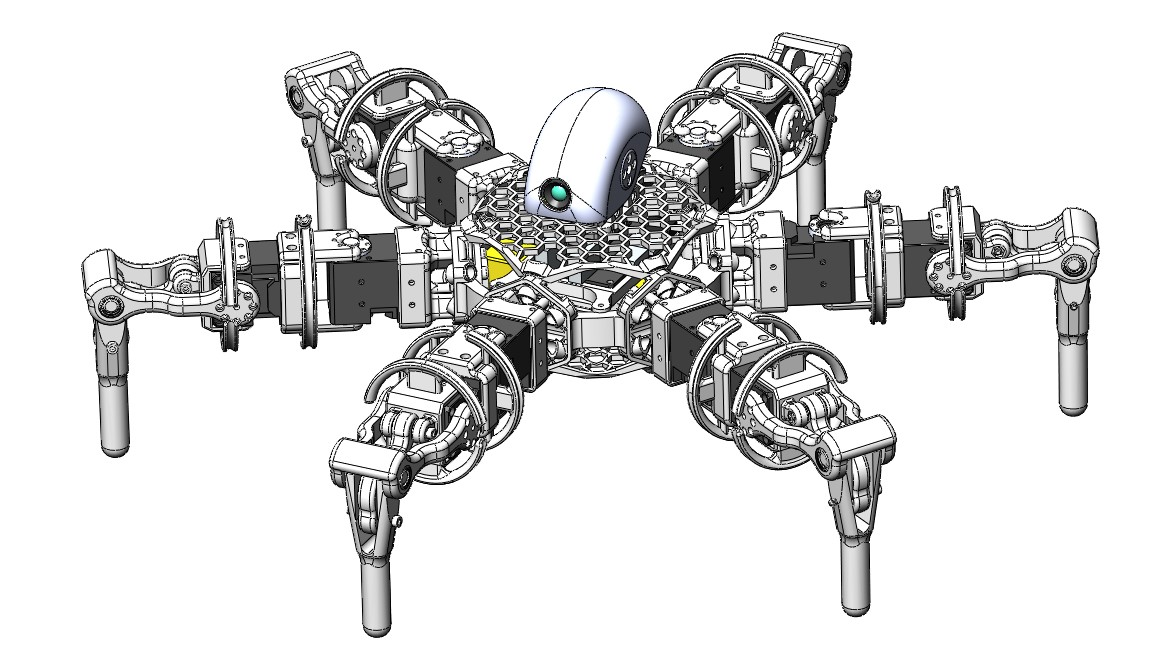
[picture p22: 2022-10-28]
3D printing STL/Head/Default_head.jpg

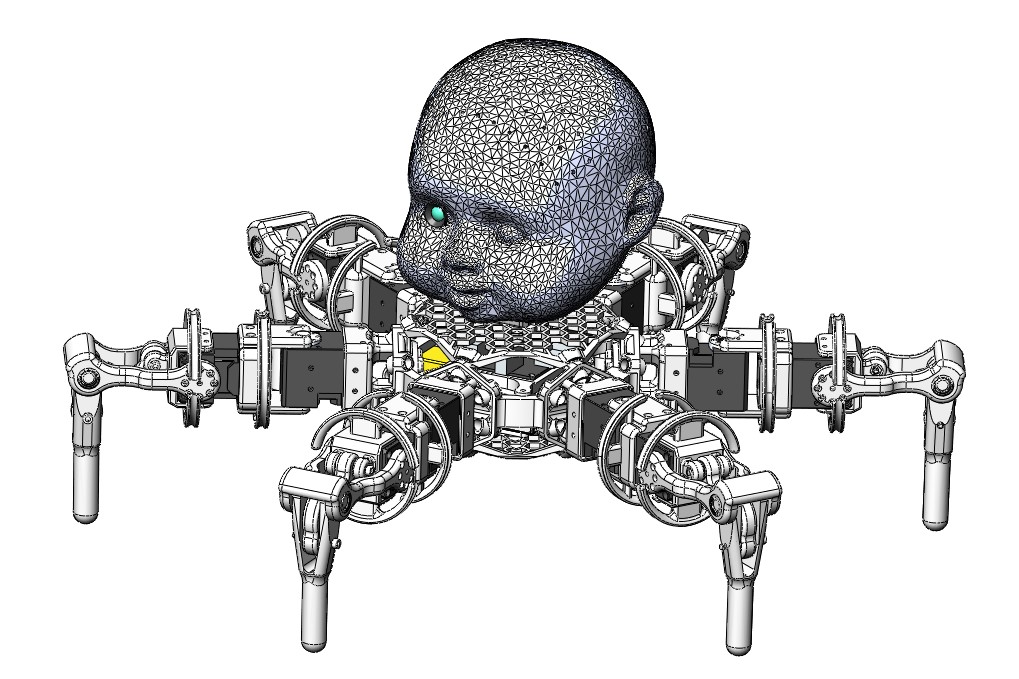
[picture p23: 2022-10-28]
3D printing STL/Head/Babyface_head.jpg

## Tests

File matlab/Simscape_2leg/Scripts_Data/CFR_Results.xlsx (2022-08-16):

 | Contact Forces Tests | 9.6.0.1072779 (R2019a) |  |  | 19-Mar-2019 07:07:34 |  | CFL v4.1
 |  |  | Linear, No Friction |  | Linear, Stick-Slip C |  | Nonlin., No Friction |  | Nonlin., Stick-Slip C
# | Model | Stop Time | # Steps | Sim Time | # Steps | Sim Time | # Steps | Sim Time | # Steps | Sim Time
1 | Collision_01_Ball_Infinite_Plane | 6.00 | 2388 | 1.18 | 2388 | 0.39 | 2388 | 0.47 | 2388 | 0.33
2 | Collision_02_Disk_Finite_Plane_Fixed | 4.00 | 669 | 0.56 | 935 | 0.18 | 718 | 0.15 | 1020 | 0.16
3 | Collision_03_Disk_Finite_Plane_Spin | 1.50 | 298 | 0.29 | 370 | 0.11 | 317 | 0.07 | 398 | 0.08
4 | Collision_04_Disks_in_Box | 3.00 | 3726 | 4.08 | 4928 | 5.10 | 5039 | 3.11 | 6295 | 4.05
5 | Collision_05_Disk_in_Ring | 5.00 | 2071 | 0.37 | 2660 | 0.77 | 2276 | 0.56 | 2954 | 0.65
6 | Collision_06_Catapult | 1.20 | 612 | 0.21 | 579 | 0.17 | 747 | 0.17 | 602 | 0.21
7 | Collision_07_Ball_Finite_Plane_Float | 1.50 | 210 | 0.08 | 213 | 0.04 | 221 | 0.06 | 223 | 0.05
8 | Collision_08_Compare_Forces | 5.00 | 9225 | 5.33 | 17963 | 6.91 | 10816 | 3.80 | 21376 | 10.73
9 | Friction_01_Box_on_Ramp_Constraint | 10.00 | 1137 | 0.17 | 1137 | 0.10 | 1137 | 0.09 | 1137 | 0.10
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

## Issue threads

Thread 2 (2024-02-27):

BOM request

h3rb, 2024-02-27:
You guys provide a lot of the required files for a hobbyist or researcher to build this device, but you don't provide a BOM.  Could you provide a BOM or a link to a BOM?

sanky1234, 2025-01-29:
https://github.com/uiuckimlab/Snapbot/blob/master/3D%20printing%20STL/BOM%20(Part%20list).pdf

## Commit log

2021-10-15 Snapbot URDF
    [Body.STL, Camera_module_1.STL, Camera_module_2.STL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]
2022-08-16 Simulation & URDF
    [Body - cover_V4-1.STL, Body - cover_top_V4-1.STL, Body.STL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]
2022-08-16 BOM location moved to STL folder
2022-08-17 reconfigured folders, tested on ubuntu 20.04 ROS noetic
    [Body - cover_V4-1.STL, Body - cover_top_V4-1.STL, Body.STL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]
2022-08-18 3D printing STL folder added
    I restored the folder "3D printing STL" since the meshes includes some parts that is not necessary for building the robot (bearings, camera, magnets). Also the folder contains the PDF document for th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
    [Body - cover_V4-1.STL, Body - cover_top_V4-1.STL, Camera_bracket_1.STL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]
2022-10-28 Babyface STL & URDF added
    [Babyface_Face.STL, Babyface_bracket.STL, Body.STL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]
2022-10-28 Revert "Babyface STL & URDF added"
    This reverts commit a2dd92791732e5d41ce8624df0539338eb94754d.
    [Babyface_Face.STL, Babyface_bracket.STL, Body.STL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]
2022-10-28 Revert "Revert "Babyface STL & URDF added""
    This reverts commit aec7143cbe81e5ab465489fca4615a05b7ec863e.
    [Babyface_Face.STL, Babyface_bracket.STL, Body.STL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]
